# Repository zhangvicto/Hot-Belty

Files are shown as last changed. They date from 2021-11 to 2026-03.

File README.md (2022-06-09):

# Hot Belty
A high temperature conveyor belt low-cost open-source 3d-printer for printing engineering plastics such as PEKK/PEEK/PEI. 

# Current Progress
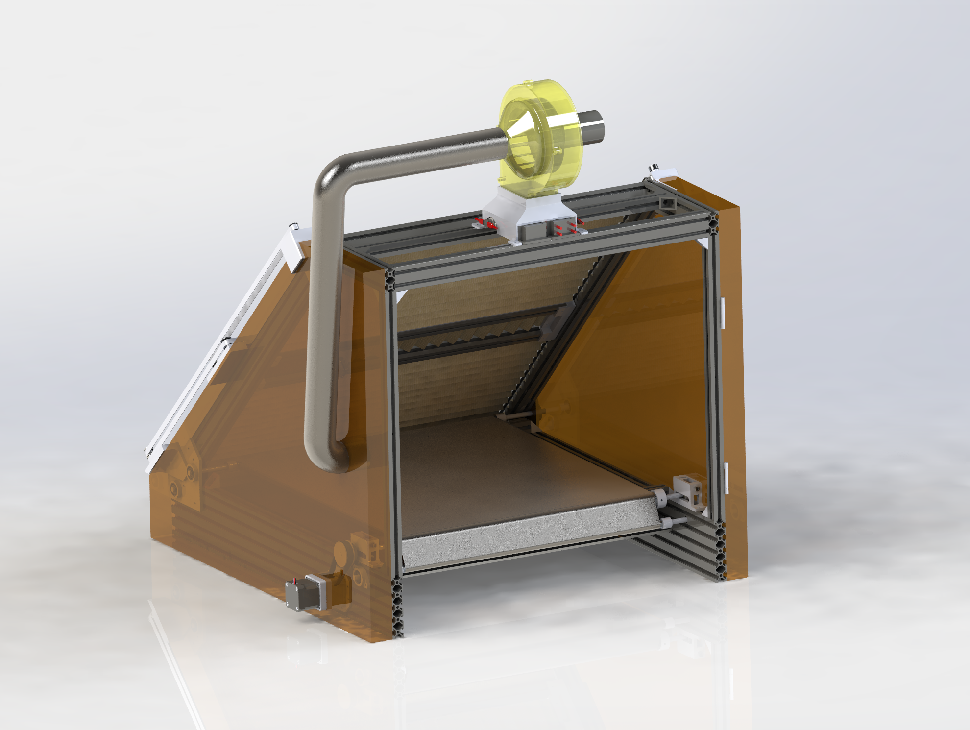
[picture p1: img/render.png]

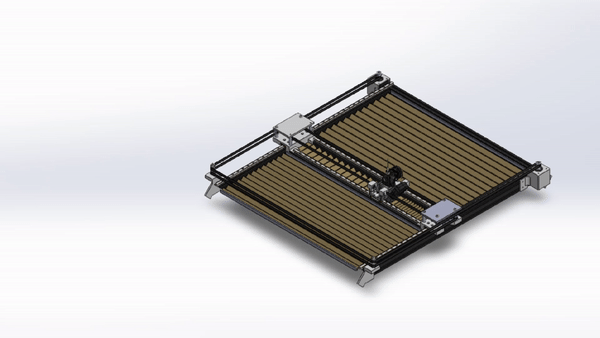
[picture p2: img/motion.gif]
gif

https://www.youtube.com/shorts/wCqyctF1fq8

- [x] Find improvements from previous Design
- [x] Part Selection
- [x] Belt Design
- [x] CAD design
- [x] Material purchasing
- [x] Testing Enclosure Heating
- [x] Building
- [x] Firmware Software Implementation
- [x] Enclosure Software
- [ ] Troubleshooting and Tuning (5%)
- [ ] Enclosure Extension Design (20%)

# Printer Specification Goals
## 24V System
Since 24V components cost the same as 12V, we can use thinner wires which are cheaper. 24V components are also more readily available compared to 12V.

## Enclosure Temp
The focus is on printing PEKK/PEEK and PEI, which are best printed at an enclosure temperature between 150C - 200C. It is also achievable with temperature of 135C with very careful tuning. Since the conveyor belt does not provide the best bed adhesion, it is better to have a higher temperature at which the plastic material can be properly 3d-printed to prevent failures and warping. 

## Bed Temperature
A bed temperature of 200C+ is absolutely needed for printing PEKK/PEEK/PEI, especially since the belt does not transfer all of the heat, the bed heater will need to reach near 250C to ensure bed adhesion. A 1200W AC 120V 400mm square silicone heater is used to speed up heating and it will be sufficient to heat up the 450mm square aluminum bed. The bed heats up to 60C in around 20 seconds. 

# Electronics
An off-the-shelf 3d-printer motherboard/controller will be used for this printer. Relays will be used to control the bed and enclosure as they are powered directly from mains. Limit switches will be used as end stops for the X and Y axes, the belt will have no end stop. 

## Design Methodology
# Iterative & Simple
The goal of the design is to come close to a finalized machine as possible before actual fabrication. During this design phase, the parts will be designed at first to be minimally viable, then optimized in terms of appearance and weight. The optimization is either done through a combination between finite element analysis (FEA) and using design for manufacturing and assembly. 

# Parts Fabrication 
## Belt Fabrication
1. Cut to size with aviation snips. 
2. Tape the ends together with Kapton tape. 

## Frame Parts
Most parts will be 3d-printed in polycarbonate, nylon, or PETG. 

## Open-Source Licenses
OS

---
Special thanks to Dr. Pearce and the FAST Laboratory.

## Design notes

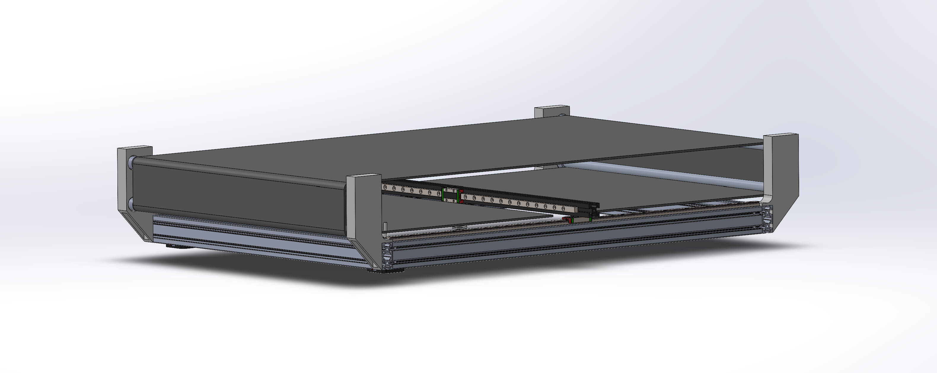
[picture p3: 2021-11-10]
img/xy_gantry_v1.png

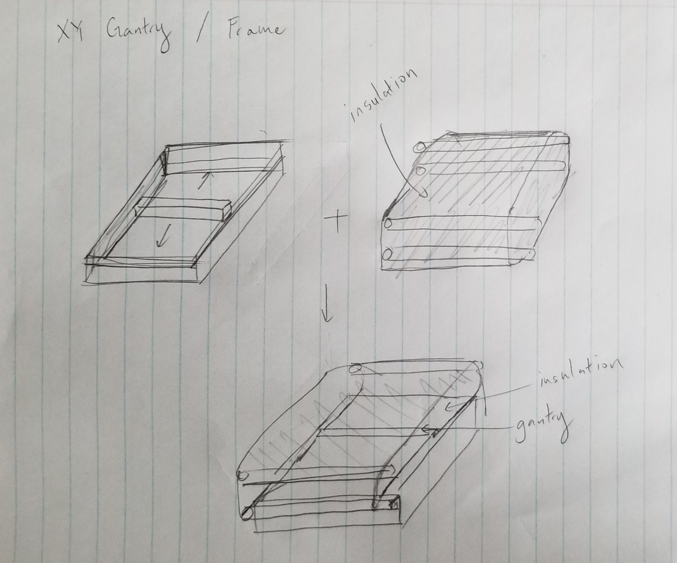
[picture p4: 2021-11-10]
img/drawing1.jpg

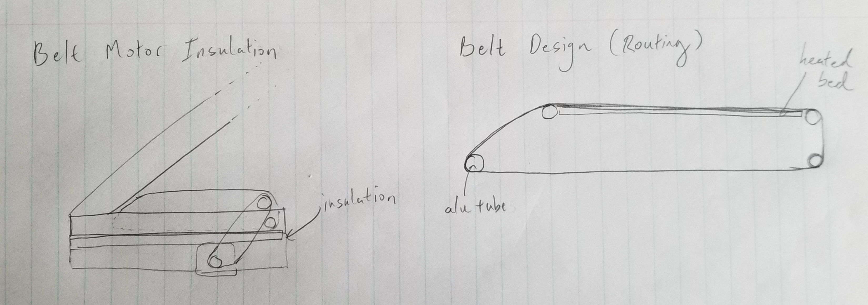
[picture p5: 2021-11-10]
img/drawing2.jpg

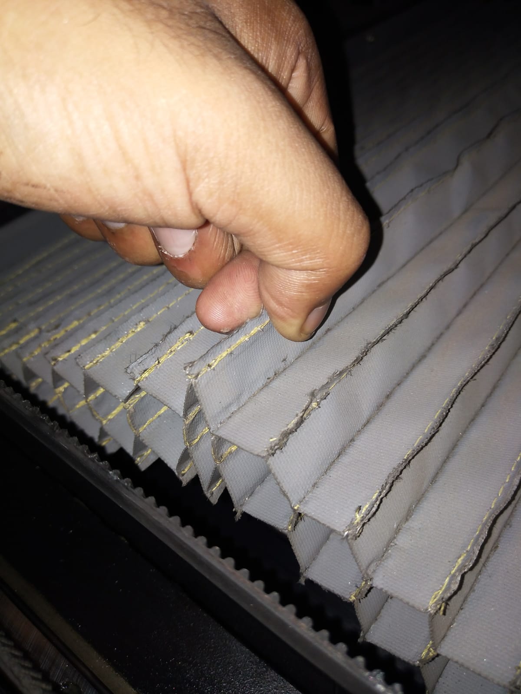
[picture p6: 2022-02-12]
cad_v2/reference-images/fortus450-bellow.jpeg

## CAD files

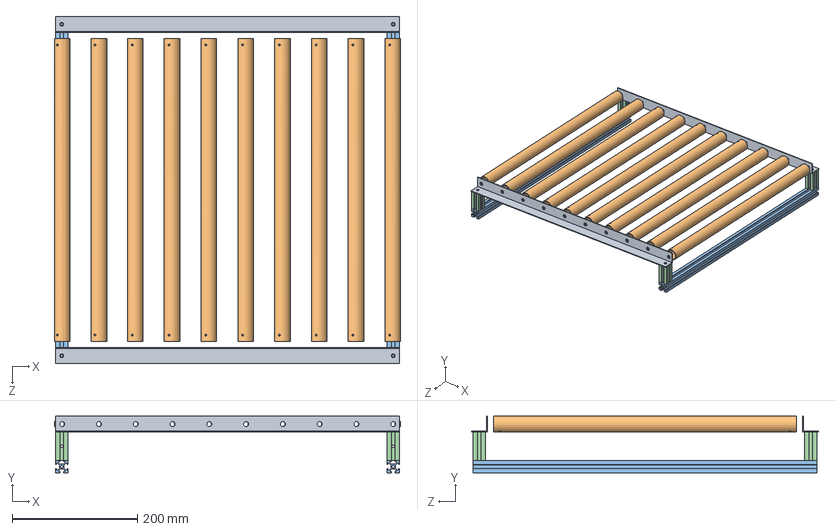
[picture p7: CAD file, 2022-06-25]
CAD/enclosure-extension/extension.SLDASM
553.6 x 90.7 x 554.8 mm
alu-angle x 2
alu_tube_actuated_1in x 10
bottom-extrusion x 2
feet x 4

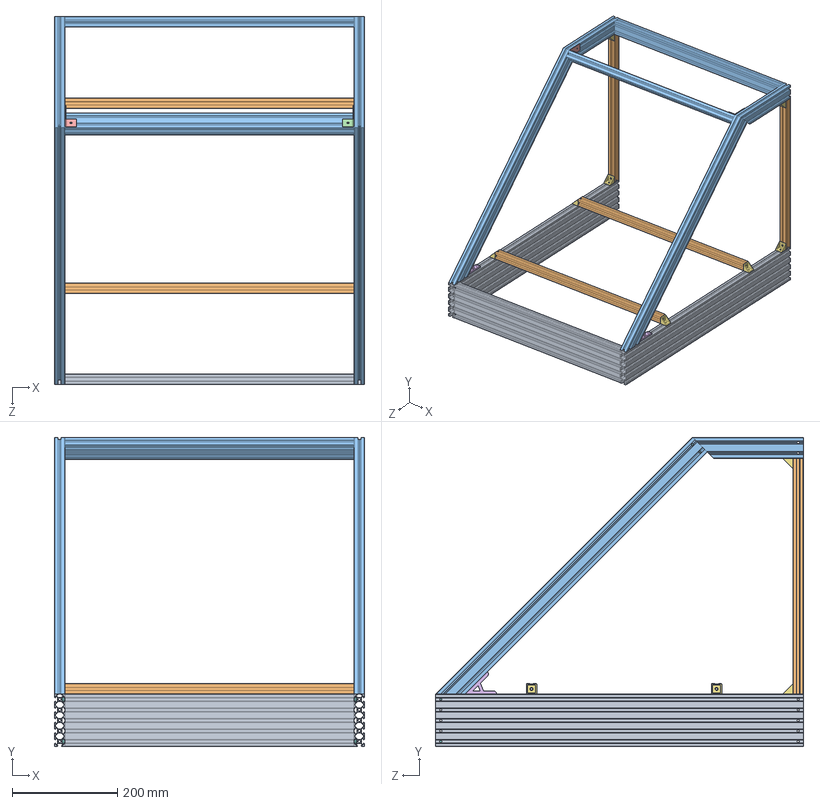
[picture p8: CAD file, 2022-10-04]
CAD/printer/frame/printer-frame.SLDASM
590.0 x 588.6 x 700.0 mm
20100-extrusion x 3
2020-extrusion x 4
2040-extrusion x 6
angled-alu-bracket
angled-alu-bracket-mirrored
frame-angled-support x 2
2020-angle-bracket x 8
m6-buttonhead-screw x 8

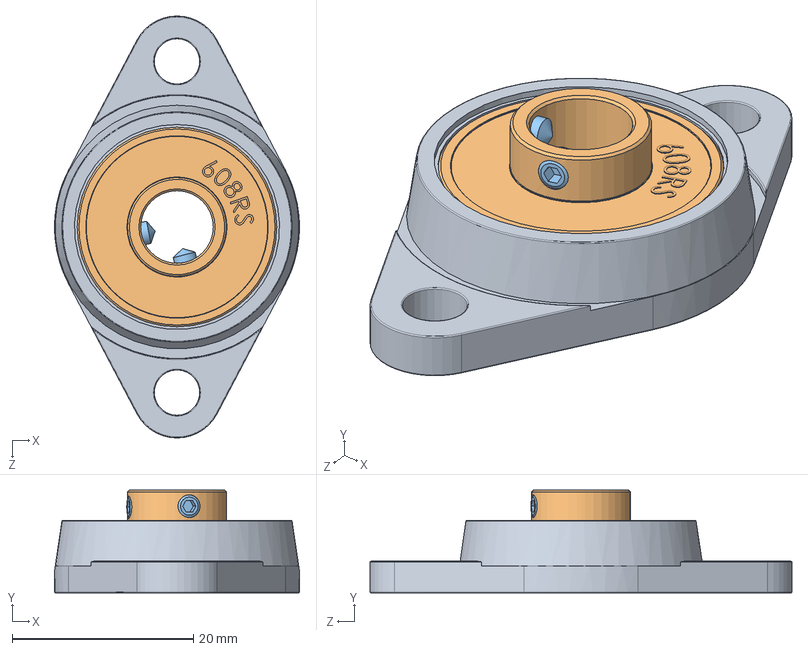
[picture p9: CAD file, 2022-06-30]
CAD/printer/motion/bearings/flange-bearings/kfl08/KFL08.SLDASM
27.0 x 11.4 x 46.5 mm
KFL08
608RS
MOSCAM2,5 x 2

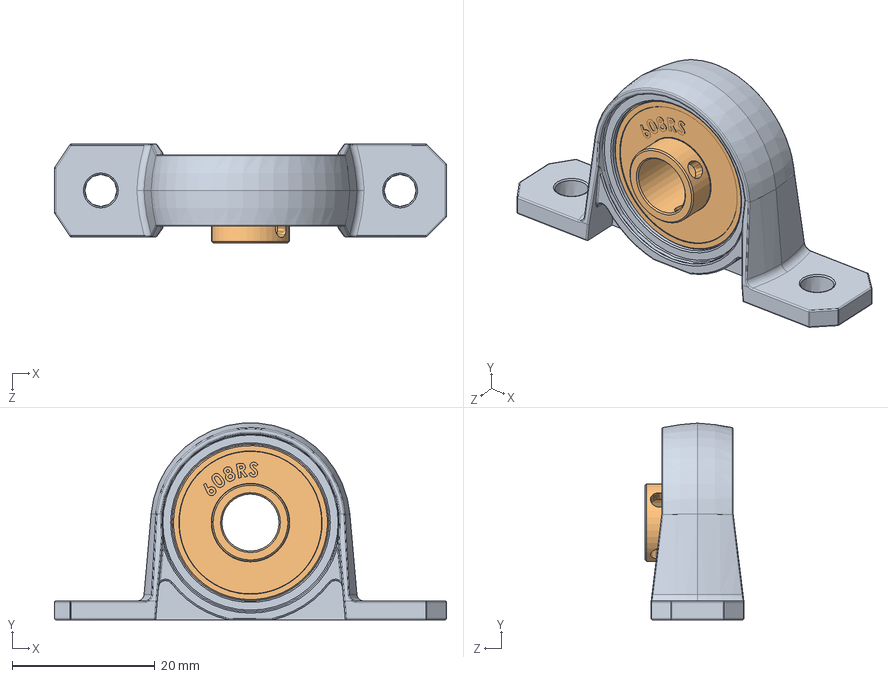
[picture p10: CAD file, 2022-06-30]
CAD/printer/motion/bearings/flange-bearings/kp08/KP08.SLDASM
55.0 x 27.6 x 13.9 mm
KP08
608RS-1

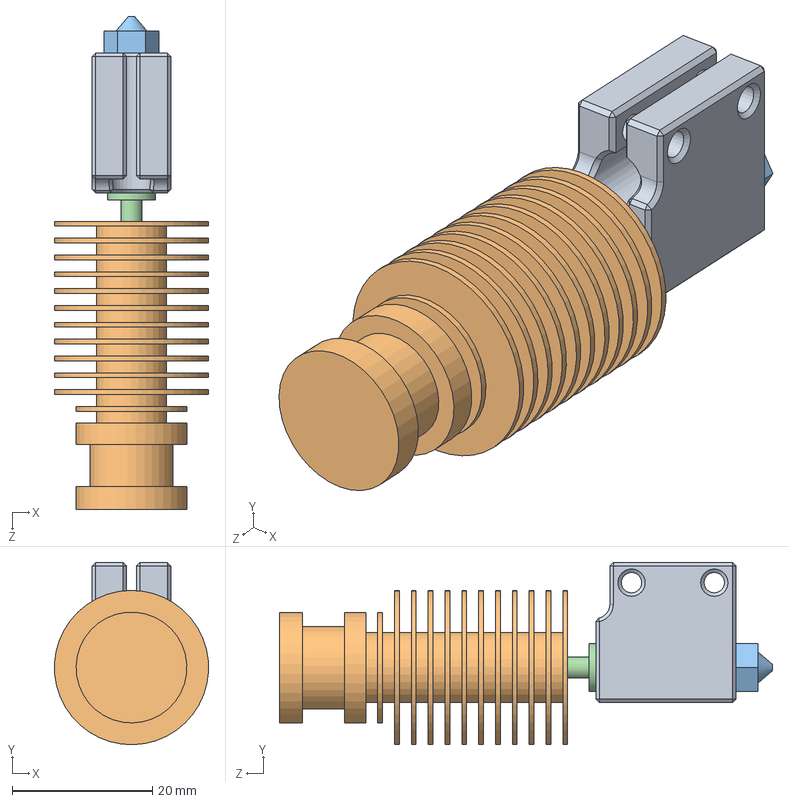
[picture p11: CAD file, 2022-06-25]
CAD/printer/toolhead/single-extruder/hotend-volcano/Hotend Volcano J-head V6.SLDASM
22.0 x 26.0 x 70.3 mm
Bloco Aquecedor
Dissipador
Bico 0.4mm
Tubo conector

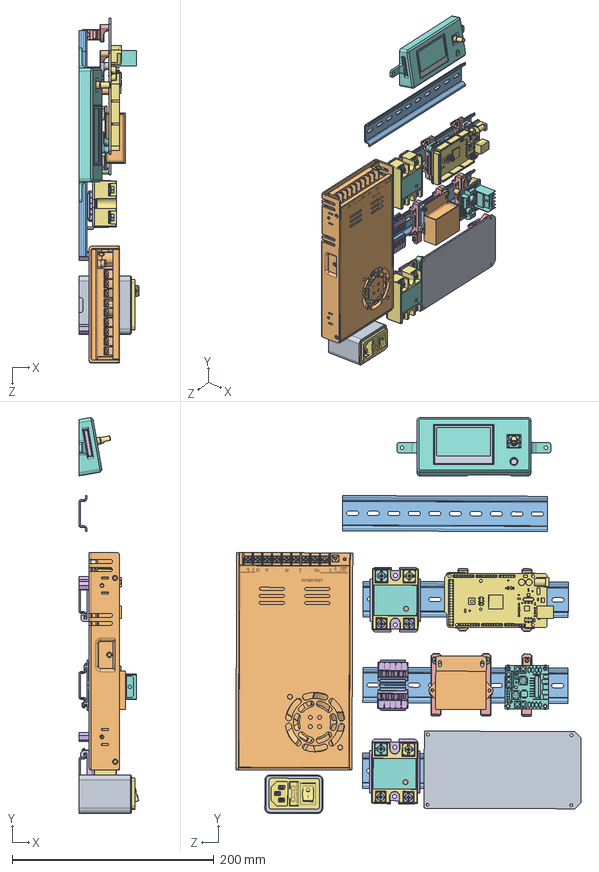
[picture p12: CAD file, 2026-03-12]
cad_v2/electronics/electronics.SLDASM
59.2 x 392.2 x 342.0 mm
motherboard-fysetc-spider
meanwell-350
din-rail x 4
board-DIN-bracket1.step
board-DIN-bracket2.step
ssr-mount-bracket.step x 2
Body.step x 4
Body002.step x 4
Body004.step x 4
Body005.step x 4
Body006.step x 4
Body007.step x 4
Body008.step x 4
Body009.step x 4
Body010.step x 4
Body011.step x 4
Body012.step x 4
Body013.step x 4
Body014.step x 4
Body015.step x 4
Body003.step x 2
wago-221-415.step x 2
arduino-mega
mega-din-mount-left
mega-din-mount-right
dc-dc-converter-24v
dc-converter-din-mount-right
dc-converter-din-mount-left
din-clip-1 x 7
nylon-spacer x 3
power-inlet-15A
l298n-motor-driver
power-inlet-enclosure
l298n-din-mount
wago-221-din-mount
display-12864mini1.step
display-12864mini2.step
display-12864mini3.step
display-12864mini4.step
display-12864mini5.step
display-12864mini6.step
display-12864mini7.step
display-12864mini8.step
display-12864mini9.step
display-12864mini10.step
display-12864mini11.step
display-12864mini12.step
display-12864mini13.step
display-12864mini14.step
display-12864mini15.step
display-12864mini16.step
display-12864mini17.step
display-12864mini18.step
display-12864mini19.step
display-12864mini20.step
display-12864mini21.step
display-12864mini22.step
display-12864mini23.step
display-12864mini24.step
display-12864mini25.step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

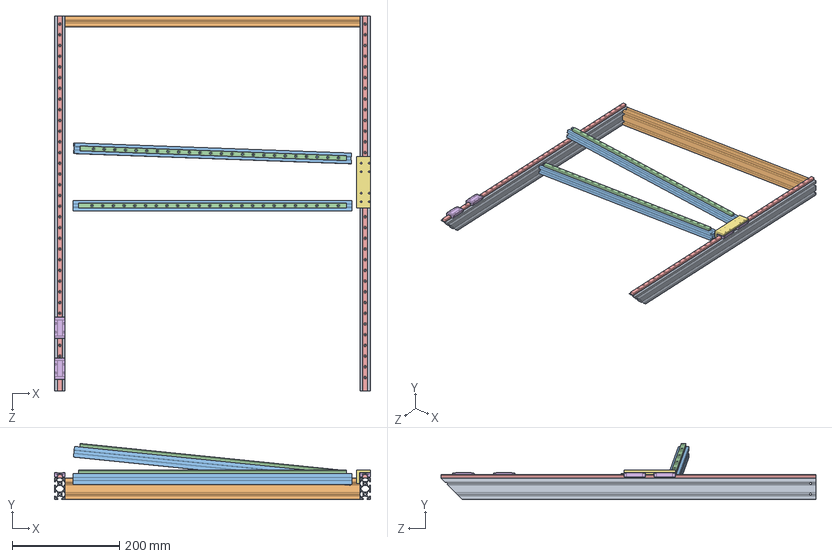
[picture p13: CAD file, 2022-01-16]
v2_cad/gantry/gantry.SLDASM
590.0 x 104.6 x 700.0 mm
2040_700mm x 2
2040_500mm
2020_500mm x 2
MGN9_500mm x 2
MGN9_700mm x 2
MGN9-H x 4
xgantrymount

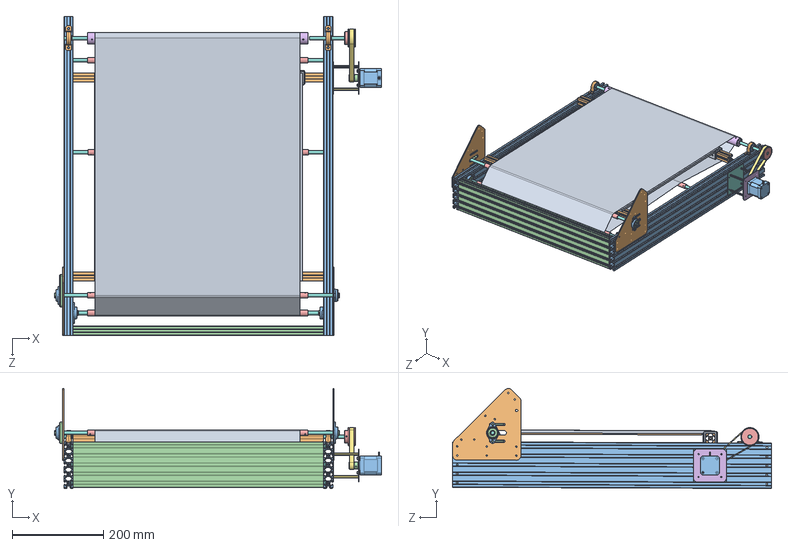
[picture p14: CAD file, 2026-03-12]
cad_v2/belt_frame/belt_frame.SLDASM
718.8 x 219.8 x 700.4 mm
alu_bed
2020_550mm_bed_mount x 2
20100_700mm x 2
20100_550mm
alu_tube_500mm x 4
alu_tube_actuated_1in
alu_tube_inner_lock x 6
steel_rod_8mm x 10
Belt1-2^belt_frame
silicone_heater
belt_motor
2GT_20T_Toothed_Pulley_9mm
GT2_60T_8B
alu_tube_inner_lock_1in
Belt2-6^belt_frame
m6-button-15 x 6
bed-mount
frame_bracket_alu x 2
KFL08 x 4
608RS x 4
MOSCAM2,5 x 8
belt-motor-mount-alu
m3-standoff x 4
belt-motor-mount-extrusion-side-alu
m3-socket-8 x 4
KP08 x 2
608RS-1 x 2
flange-bearing-adapter

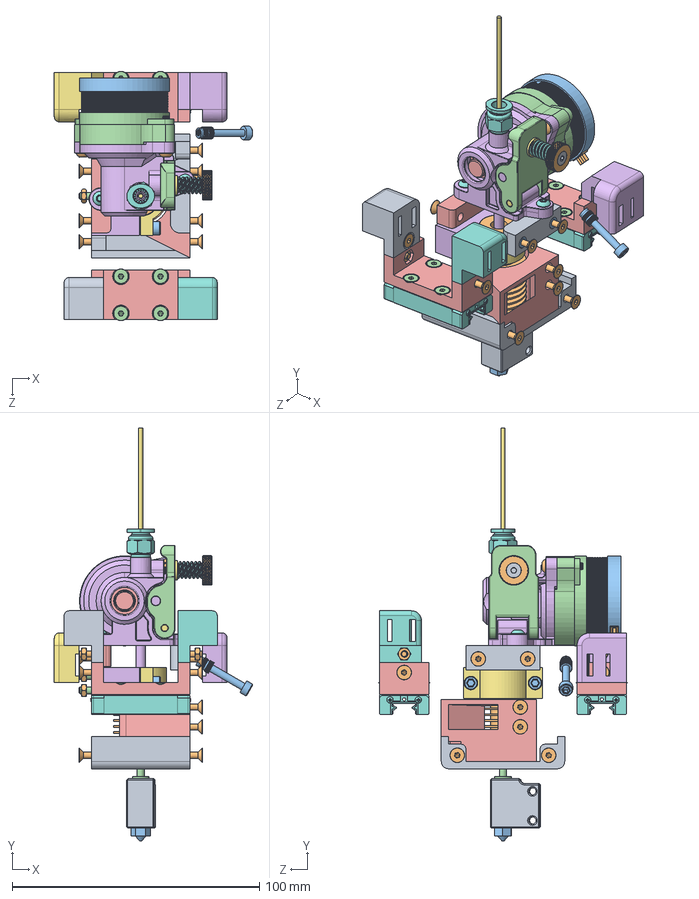
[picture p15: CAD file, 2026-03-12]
cad_v2/gantry/Hotend-Assembly.SLDASM
80.4 x 167.2 x 100.9 mm
Bloco Aquecedor
Dissipador
Bico 0.4mm
Tubo conector
hotend-assem-mount x 2
v6-adapter-block
v6-adapter-mount
MGN9-H x 2
hotend-assem-bottom
m3-nut x 16
m3-socket-20 x 3
m3-countersunk-8 x 8
orbitor-mount-left
PTFE Exit.step
92095A182.step x 2
LatchSleve.step
92095A119.step x 2
insert M3.step
Gear Housing (65 teeth).step
90940A412.step
Spring v1.step
92125A138.step
KnurledNut.step
Component4.step
Component5.step
Component6.step
Component7.step
Component8.step
Component9.step
Component10.step
Component11.step
Component12.step
Component13.step
Component14.step
Component15.step x 2
Component16.step x 2
Component17.step x 2
Component18.step x 2
Component19.step
T10 SpurGear.step
Latch.step
SpiderShaft.step
Housing 1.5.step
LatchShaft.step
orbitor-mount-right
m3-countersunk-10 x 18
m3-heatset-large x 3
m3-socket-12 x 2
v6-cooling-cover
belt-clamp-lower
belt-clamp-lower-right
belt-clamp-upper-left
belt-clamp-upper-right

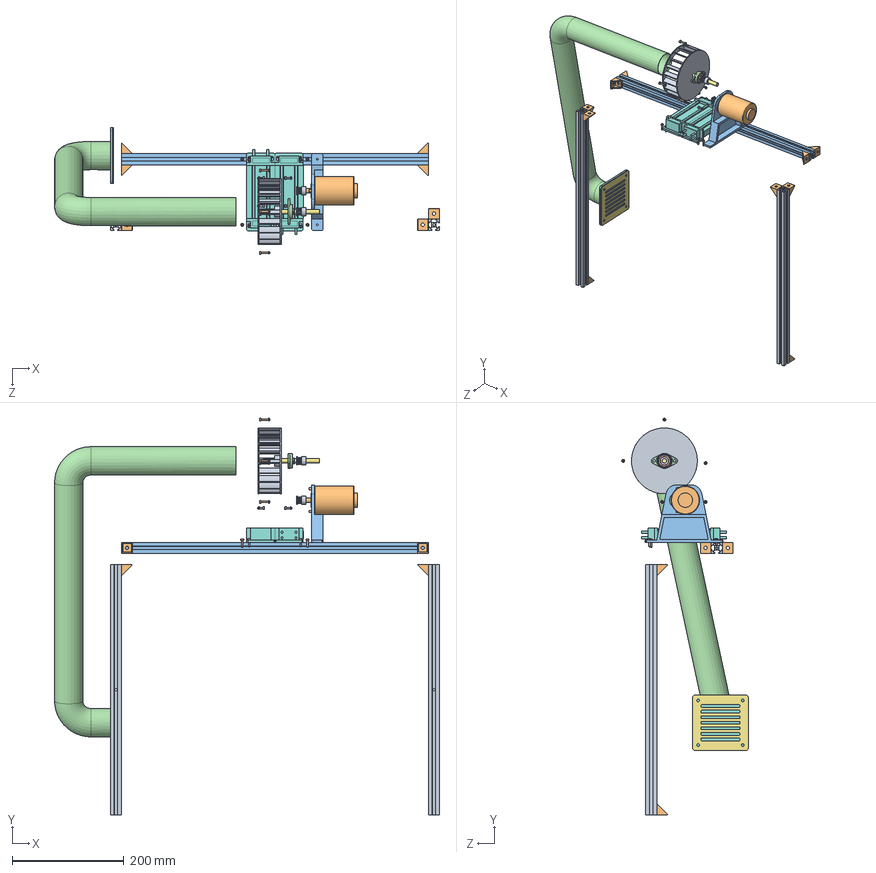
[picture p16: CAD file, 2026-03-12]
cad_v2/blower/heater-blower-assembly.SLDASM
690.1 x 711.2 x 227.0 mm
impeller
m3-socket-16 x 5
m3-nut x 9
KFL08
608RS
MOSCAM2,5 x 2
steel-rod-8mm-100mm
ptc_heating_110V_500W x 2
2020_455mm x 2
angle_bracket x 10
2020_horizontal
duct
m3-socket-8 x 8
m3-socket-10 x 4
tube-mount-filter-side
activated-carbon-filter
gt2-pulley-20t-6mm x 2
xd3420_motor
motor-mount

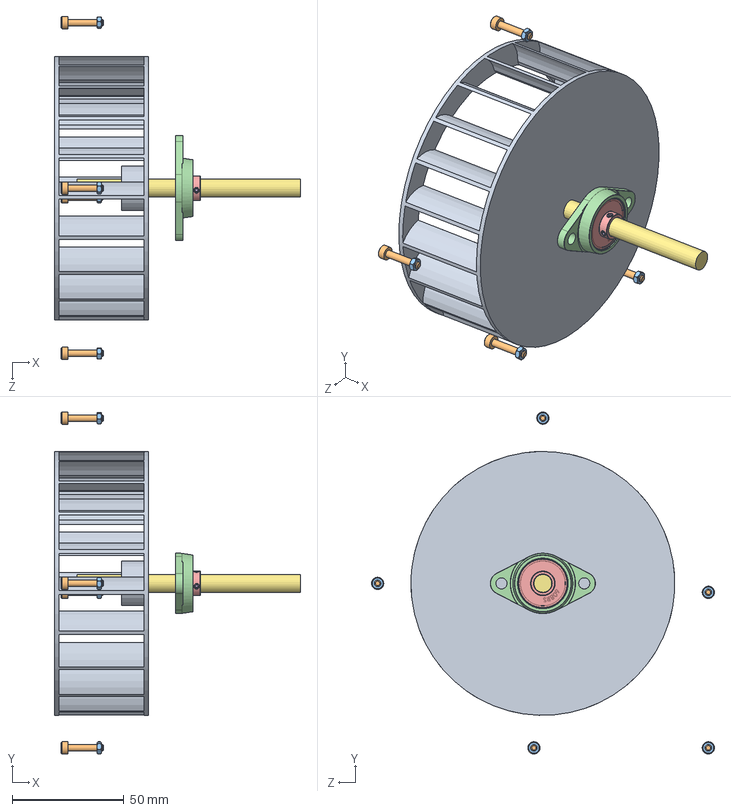
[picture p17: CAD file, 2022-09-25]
cad_v2/blower/blower.SLDASM
110.0 x 152.9 x 153.4 mm
impeller
m3-socket-16 x 5
m3-nut x 5
KFL08
608RS
MOSCAM2,5 x 2
steel-rod-8mm-100mm

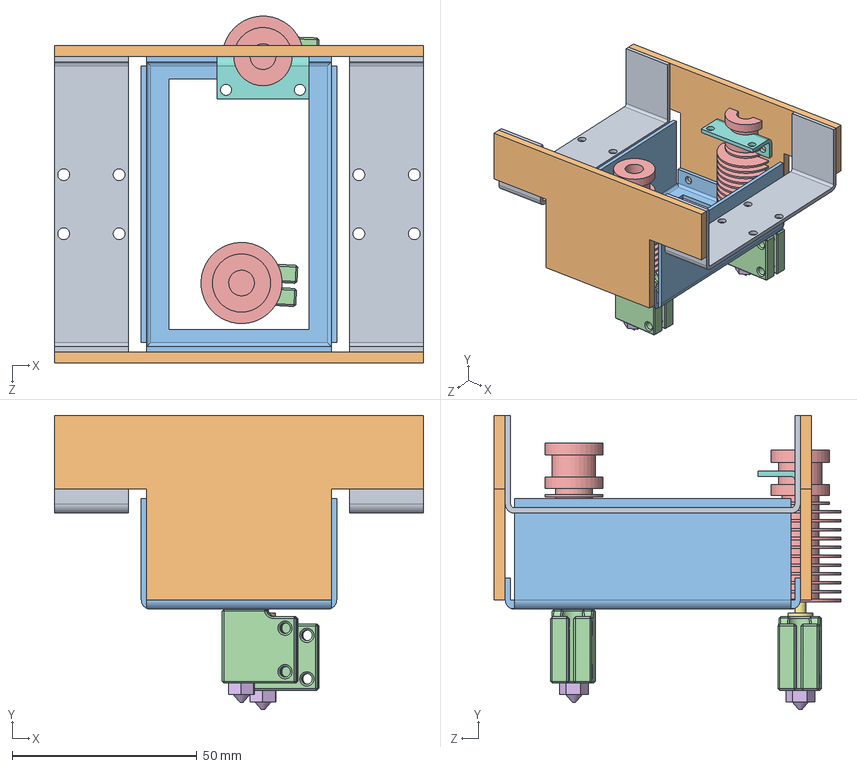
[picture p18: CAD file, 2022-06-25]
CAD/printer/toolhead/dual-extruder/dual-extruder.SLDASM
100.0 x 79.7 x 94.0 mm
h-mount x 2
dual-layer-side-plate x 2
bottom-plate
Bloco Aquecedor x 2
Dissipador x 2
Bico 0.4mm x 2
Tubo conector x 2
hotend-mount-bracket

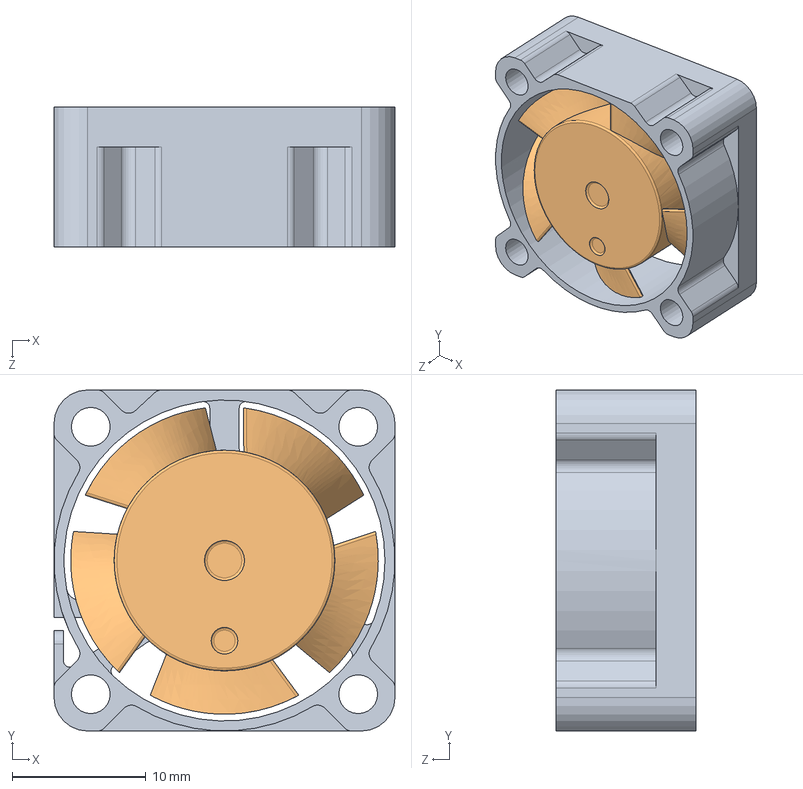
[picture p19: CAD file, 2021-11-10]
CAD/printer/toolhead/single-extruder/hotend-volcano/25x25x10_fan.SLDASM
25.5 x 25.5 x 10.5 mm
Body.step
Blades.step

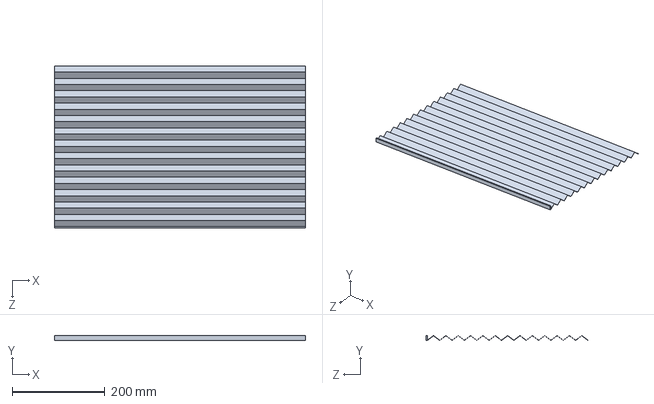
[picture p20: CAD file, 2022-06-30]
cad_v2/gantry/bellow_main_2.SLDPRT
540.0 x 10.6 x 348.8 mm

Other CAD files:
cad_v2/belt_frame/kp08/KP08.SLDASM
cad_v2/other/kfl08/KFL08.SLDASM
cad_v2/gantry/bellow_main.SLDPRT
cad_v2/belt_frame/roller-tensioner-main.SLDPRT
CAD/enclosure-extension/frame/alu-angle.SLDPRT
CAD/enclosure-extension/frame/aluminum-extrusion.SLDPRT
CAD/enclosure-extension/frame/feet.SLDPRT
CAD/enclosure-extension/insulation/horizontal-insulation.SLDPRT
CAD/enclosure-extension/insulation/vertical-insulation.SLDPRT
CAD/enclosure-extension/motion-components/rollers/alu_tube_actuated_1in.SLDPRT
CAD/printer/bed/aluminum-bed.SLDPRT
CAD/printer/blower/activated-carbon-filter.SLDPRT
CAD/printer/blower/blower-bottom.SLDPRT
CAD/printer/blower/blower-mount.SLDPRT
CAD/printer/blower/duct.SLDPRT
CAD/printer/blower/impeller.SLDPRT
CAD/printer/blower/tube-mount-filter-side.SLDPRT
CAD/printer/blower/tube-mount.SLDPRT
CAD/printer/electrical/heaters/ptc_heating_110V_500W.SLDPRT
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

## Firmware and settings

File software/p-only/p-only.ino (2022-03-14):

//NOTES: 
//P-Only Controller
//CO = CObias + Kc*e(t)
//CObias = controller bias or null value
//Kc = controller gain, a tuning parameter
//e(t) = controller error = SP – PV
//SP = set point
//PV = measured process variable
//https://controlguru.com/the-p-only-control-algorithm/
//https://controlguru.com/design-and-tuning-recipe-must-consider-nonlinear-process-behavior/

const int coBias = 20;
int co;
int kc = 2.5;
int SP;
int PV;
int e_t;

void setup() {
  // put your setup code here, to run once:

}

void loop() {
  // put your main code here, to run repeatedly:

}

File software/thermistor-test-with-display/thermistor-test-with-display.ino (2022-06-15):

//-----------------------------------------------------------------------------------------//

//THERM SETUP - B3950
// resistance at 25 degrees C
#define THERMISTORNOMINAL 100000
// temp. for nominal resistance (almost always 25 C)
#define TEMPERATURENOMINAL 25
// how many samples to take and average, more takes longer
// but is more 'smooth'
#define NUMSAMPLES 5
// The beta coefficient of the thermistor (usually 3000-4000)
#define BCOEFFICIENT 3950
// the value of the 'other' resistor
#define SERIESRESISTOR 100000

const int thermPin1 = A0;
const int thermPin2 = A1;
const int thermPin3 = A2;
const int thermPin4 = A3;


//TIMING
const int delayTime = 5000;
int prevTime = 0;

int bangPrevTime = 0;


//HEATER
const int heaterPin = 22;
const int buttonPin = 3; //30 for mega
int buttonState = 0;

//SWITCH
const int switchPin = 40;
int switchState = 0;

//DEBOUNCE
//unsigned long lastDebounceTime = 0;
//unsigned long debounceDelay = 50;


//MOTOR
const int motorPWM = 4;
const int motorIn1 = 23;
const int motorIn2 = 24;
int motorSpeed = 8;


//DISPLAY
#include <Adafruit_GFX.h>    // Core graphics library
#include <Adafruit_ST7789.h> // Hardware-specific library for ST7789
#include <SPI.h>             // Arduino SPI library

//ST7789 TFT module connections
#define TFT_CS    10  // define chip select pin
#define TFT_DC     9  // define data/command pin
#define TFT_RST    8  // define reset pin, or set to -1 and connect to Arduino RESET pin

//Initialize Adafruit ST7789 TFT library
Adafruit_ST7789 tft = Adafruit_ST7789(TFT_CS, TFT_DC, TFT_RST);
float p = 3.1415926;

//BANG BANG
const int goalTemp = 80;
const int hysteresis = 4;
int lastTemp = 0;
int isRising = 0;
int isDropping = 0;
int cooling = 0;


//-----------------------------------------------------------------------------------------//


void setup(void) {
  //heater
  pinMode(heaterPin, OUTPUT);
  digitalWrite(heaterPin, LOW);


  //button
  pinMode(buttonPin, INPUT_PULLUP);

  //switch
  pinMode(switchPin, INPUT);


  //Motor - remember to ground power supply with arduino
  pinMode(motorPWM, OUTPUT);
  pinMode(motorIn1, OUTPUT);
  pinMode(motorIn2, OUTPUT);
  //stop motor
  analogWrite(motorPWM, 0);
  digitalWrite(motorIn1, LOW);
  digitalWrite(motorIn2, LOW);


  //DISPLAY
  tft.init(240, 240, SPI_MODE2);
  tft.setRotation(2);
  tft.fillScreen(ST77XX_BLACK);


  //Serial.begin(9600);
  analogReference(EXTERNAL);
}

void loop(void) {
  float temperature1;
  float temperature2;
  float temperature3;
  float temperature4;

  //Motor start
  digitalWrite(motorIn1, LOW);
  digitalWrite(motorIn2, HIGH);
  analogWrite(motorPWM, map(motorSpeed, 0, 100, 75, 255));


  //Temperature Conversion
  int time_now = millis();
  if (time_now - prevTime > delayTime) {

    temperature1 = convert(takeSamples(thermPin1));
    temperature2 = convert(takeSamples(thermPin2));
    temperature3 = convert(takeSamples(thermPin3));
    temperature4 = convert(takeSamples(thermPin4));

    float temperatureAverage = (temperature1+temperature2+temperature3+temperature4)/4;

//    Serial.print("T1 ");
//    Serial.print(temperature1);
//    Serial.println(" C");
//
//    //IS INSTALLED?
//    Serial.print("T2 ");
//    Serial.print(temperature2);
//    Serial.println(" C");
//
//    Serial.print("T3 ");
//    Serial.print(temperature3);
//    Serial.println(" C");
//
//    Serial.print("T4 ");
//    Serial.print(temperature4);
//    Serial.println(" C");

    //Squares
    tft.drawRoundRect(10, 34, 106, 40, 5, ST77XX_WHITE);
    tft.fillRoundRect(10, 34, 106, 40, 5, ST77XX_WHITE);
    tft.drawRoundRect(124, 34, 106, 40, 5, ST77XX_WHITE);
    tft.fillRoundRect(124, 34, 106, 40, 5, ST77XX_WHITE);
    tft.drawRoundRect(10, 82, 106, 40, 5, ST77XX_WHITE);
    tft.fillRoundRect(10, 82, 106, 40, 5, ST77XX_WHITE);
    tft.drawRoundRect(124, 82, 106, 40, 5, ST77XX_WHITE);
    tft.fillRoundRect(124, 82, 106, 40, 5, ST77XX_WHITE);

    //Temperature
    drawtext("Temperature", ST77XX_WHITE, 2.5, 55, 10);
    drawtext("Sensor 1 " , ST77XX_BLACK, 2, 17, 39);
    drawfloat(temperature1, ST77XX_BLACK, 2, 28, 54); //change
    drawtext("C", ST77XX_BLACK, 2, 88, 54);

    drawtext("Sensor 2 " , ST77XX_BLACK, 2, 130, 39);
    drawfloat(temperature2, ST77XX_BLACK, 2, 141, 54); //change
    drawtext("C", ST77XX_BLACK, 2, 201, 54);

    drawtext("Sensor 3 " , ST77XX_BLACK, 2, 17, 87);
    drawfloat(temperature3, ST77XX_BLACK, 2, 28, 102); //change
    drawtext("C", ST77XX_BLACK, 2, 88, 102);

    drawtext("Sensor 4 " , ST77XX_BLACK, 2, 130, 87);
    drawfloat(temperature4, ST77XX_BLACK, 2, 141, 102); //change
    drawtext("C", ST77XX_BLACK, 2, 201, 102);

    //Chamber Status
    drawtext("Chamber Status", ST77XX_WHITE, 2.5, 35, 135);
    
    
    //default
    //if button not pressed
    if (buttonState == 0) {
      tft.fillCircle(40, 175, 15, ST77XX_GREEN);
      tft.drawCircle(40, 175, 15, ST77XX_WHITE);
      tft.drawCircle(40, 175, 14, ST77XX_WHITE);
      tft.drawCircle(40, 175, 13, ST77XX_WHITE);
      drawtext("!", ST77XX_WHITE, 2.5, 36, 168);
      tft.fillRect(80, 192, 140, 40, ST77XX_BLACK);
      drawtext("Idling at", ST77XX_WHITE, 2.5, 68, 168);
      drawfloat(temperatureAverage, ST77XX_WHITE, 2.5, 80, 192);
      drawtext("C", ST77XX_WHITE, 2.5, 150, 192); //use average
    } else if (buttonState == 1) {
      //heating
     tft.fillCircle(40, 175, 15, ST77XX_RED);
     tft.drawCircle(40, 175, 15, ST77XX_WHITE);
     tft.drawCircle(40, 175, 14, ST77XX_WHITE);
     tft.drawCircle(40, 175, 13, ST77XX_WHITE);
     drawtext("!", ST77XX_WHITE, 2.5, 36, 168);
     drawtext("Heating to", ST77XX_WHITE, 2.5, 65, 168);
     drawtext("180", ST77XX_WHITE, 3, 85, 192);
     drawtext("C", ST77XX_WHITE, 3, 145, 192);
    } else if (buttonState == 0 && cooling == 1) {
    //cooling
     tft.fillCircle(40, 175, 15, ST77XX_BLUE);
     tft.drawCircle(40, 175, 15, ST77XX_WHITE);
     tft.drawCircle(40, 175, 14, ST77XX_WHITE);
     tft.drawCircle(40, 175, 13, ST77XX_WHITE);
     drawtext("!", ST77XX_WHITE, 2.5, 36, 168);
     drawtext("Cooling to", ST77XX_WHITE, 2.5, 65, 168);
     drawtext("0", ST77XX_WHITE, 3, 100, 192);
     drawtext("C", ST77XX_WHITE, 3, 125, 192);
    }
    
    prevTime = time_now;
  }


  //-----------------------------------------------------------------------------------------//
  //                           HEATER CONTROL
  //-----------------------------------------------------------------------------------------//

  //BANG BANG CONTROL
  int bangTimeNow = millis();
  int bangCycleTime = 500; //DEFAULT cycle time
  int maxTemp = goalTemp + hysteresis;
  int minTemp = goalTemp - hysteresis;

  if ((bangTimeNow - bangPrevTime > bangCycleTime) && buttonState == 1) {

    //TAKE AVERAGE TEMP
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

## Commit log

2021-11-10 CAD Upload
    [2020_500mm.SLDPRT, 2040_500mm.SLDPRT, 2040_600mm.SLDPRT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]
2021-11-21 Update CAD
    [2020_500mm_bed_mount.SLDPRT, 2040_495mm_cut.SLDPRT, 2040_600mm_belt.SLDPRT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]
2022-01-16 v2 cad start
    [2020_500mm.SLDPRT, 2040_500mm.SLDPRT, 2040_600mm.SLDPRT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]
2022-02-13 update - gantry, tensioning, hinge
    [20100_700mm.SLDPRT, Hotend Volcano J-head V6.SLDASM, M5-nut.SLDPRT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]
2022-03-04 Blower + Insulation update
    [Hotend Volcano J-head V6.SLDASM, back-panel-insulation-temp.SLDPRT, blower-mount.SLDPRT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]
2022-03-05 Flow Sim for Blower + Gantry Update
    [5015-blower.STEP, Hotend Volcano J-head V6.SLDASM, LID1.SLDPRT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]
2022-03-05 V6 Mount
    [Hotend Volcano J-head V6.SLDASM, bellow_main.SLDPRT, bellow_main_2.SLDPRT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]
2022-03-06 Hotend Assembly Update
    [Hotend Volcano J-head V6.SLDASM, bellow_main.SLDPRT, bellow_main_2.SLDPRT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]
2022-03-07 Hotend Assembly Complete (w/o part cooling)
    [5015-blower.SLDPRT, 5015-blower.STEP, Hotend Volcano J-head V6.SLDASM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]
2022-03-13 Update + Testing
    [blower-mount.SLDPRT, blower.SLDASM, bottom.SLDPRT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]
2022-03-14 Bang Bang Control Implemented
    [hotend-assem-left.SLDPRT, top.SLDPRT, top.STL]
2022-06-07 update readme + others
    [bellow_main.SLDPRT, bellow_main_2.SLDPRT, bellow_x _2.SLDPRT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]
2022-06-11 Electronics Update
    [2020_500mm.SLDPRT, 2020_500mm_bed_mount.SLDPRT, 2020_angle_bracket_support.SLDPRT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]
2022-06-15 Electronics + Software
    [activated-carbon-filter.SLDPRT, alu_tube_holder_alt.SLDPRT, blower.SLDASM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]
2022-06-18 Extension Enclosure
    [608zz.SLDPRT, GT2_60T_8B.SLDPRT, M5x55.SLDPRT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]
2022-06-25 dual extruder WIP
    [608RS.SLDPRT, Hotend Volcano J-head V6.SLDASM, KFL08.SLDASM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]
2022-06-30 Alu Bracket for Z
    [608RS-1.SLDPRT, KFL08.SLDASM, KP08.SLDASM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]
2022-09-25 Blower Modification
    [blower-mount.SLDPRT, blower.SLDASM, bottom.SLDPRT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]
2022-10-04 Refactor + Changes
    [20100-extrusion.SLDPRT, 2020-angle-bracket.SLDPRT, 2020-extrusion.SLDPRT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]
